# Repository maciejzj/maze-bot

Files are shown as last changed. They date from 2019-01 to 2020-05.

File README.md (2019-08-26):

# MazeBot
Arduino/ATMega based mobile wheeled robot with DC motors controllers, created for a project at Silesian University of Technology.

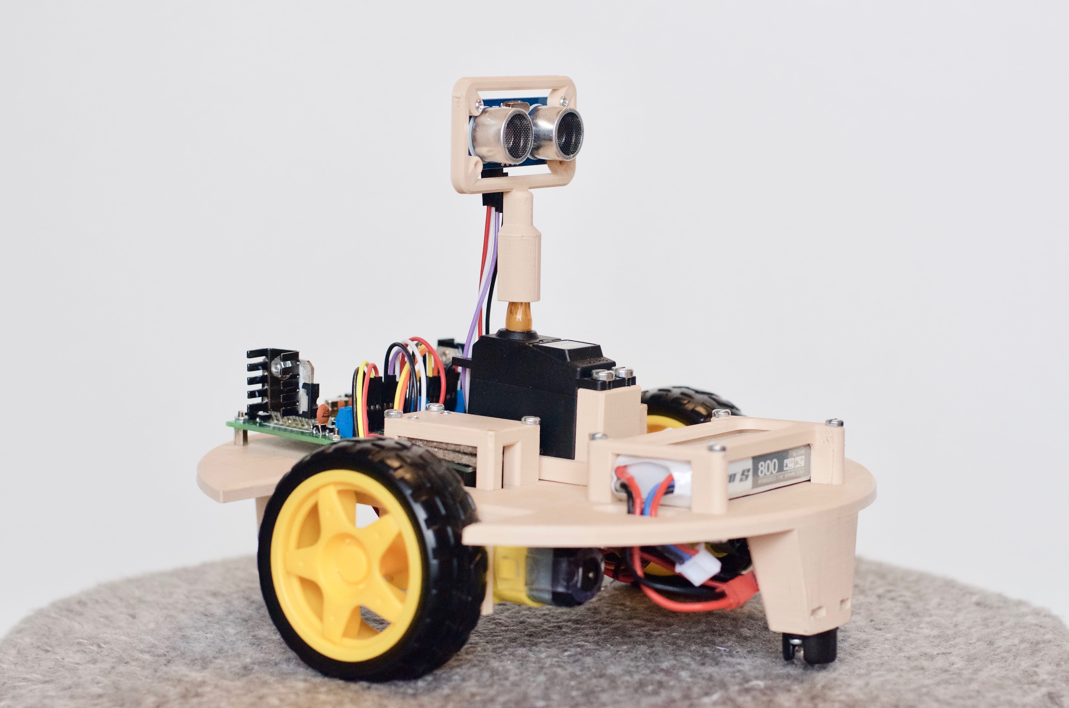
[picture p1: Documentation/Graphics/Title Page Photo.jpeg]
mazebot_demo_photo


The construction is actuated by DC motors. The robot avoids obstacles using an ultrasonic sensor mounted on top of a servo. The robot features a PI controller for synchronisation of the velocity of wheels and a cascade controller for precise turning. These control systems provide greater accuracy of movement, even with the most basic DC motors available.

The project consists of making a custom Arduino Leonardo clone PCB and designing a 3D printable chassis for the construction. Code is implemented using Arduino libraries and the bootloader.

The code and Autodesk Eagle files are stored in the GitHub repository, Autodesk Fusion 360 project files can be accessed using [Autodesk cloud mechanisms](https://a360.co/2U4947x).

Feel free to check out the documentation and [project report](https://raw.githubusercontent.com/MaciejZj/MazeBot/16cebf032a5ea0aaa41a32081933f3ef379c02ca/Documentation/POLSL_Project_Report_PL.pdf) in Polish.

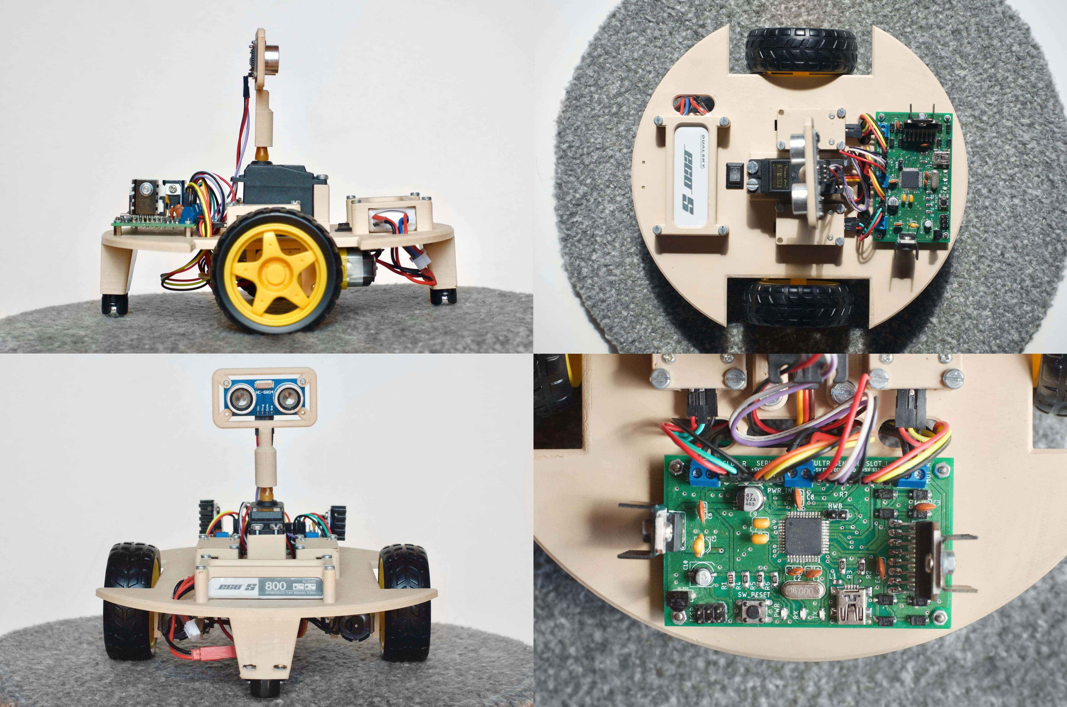
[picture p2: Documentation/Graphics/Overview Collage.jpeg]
mazebot_photo_collage


The project uses modified [nonblocking ultrasonic Arduino library](https://github.com/jazzycamel/arduino).

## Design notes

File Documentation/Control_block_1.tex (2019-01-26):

\documentclass{standalone}

\usepackage{tikz}
\usetikzlibrary{shapes, arrows}
\usetikzlibrary{arrows.meta, positioning}
\begin{document}

% Define styles
\tikzstyle{block} = [draw, rectangle, 
    minimum height=3em, minimum width=3em]
\tikzstyle{sum} = [draw, circle, inner sep=5pt, node distance=2cm]
\tikzstyle{point} = [coordinate]
\tikzstyle{pinstyle} = [pin edge={to-,thin,black}]

\begin{tikzpicture}[auto, node distance=2cm, >=latex']
	\node [point, name=input] {};
	\node [block, below of=input, label={\small Zadajnik}] (master_encoder) {Master encoder};
	\node [block, below of=master_encoder] (differ_master) {
		\begin{tabular}{c}
			Zamiana \\ $ \alpha \rightarrow \omega $
		\end{tabular}};
	\node [sum, right of=differ_master] (sum) {};
	\node [block, right of=sum, xshift=-0.5cm] (kp) {$ k_p $};
	\node [block, right of=kp, yshift=+1.25cm, xshift=0.25cm, label={\small Człon P regulatora}] (one) {$ 1 $};
	\draw [->] (kp) |- node[name=con_one] {} (one);
	\node [block, right of=kp, yshift=-1.25cm, xshift=0.25cm, label={\small Człon I regulatora}] (int) {$ \frac{1}{sT_I} $};
	\draw [->] (kp) |- node[name=con_int] {} (int);
	\node [sum, right of=sum, xshift=4cm] (sum_con) {};
	\node [block, right of=sum_con, xshift=0.25cm] (system) {Obiekt SWPS};
	\draw [->] (sum_con) -- node[name=u] {$u$} (system);
	\node [point, right of=system] (point) {};
	\node [block, below of=u, yshift=-1cm] (slave_encoder) {Slave encoder};
	\node [block, left of=slave_encoder, xshift=-1.75cm] (differ_slave) {
		\begin{tabular}{c}
			Zamiana \\ $ \alpha \rightarrow \omega $
		\end{tabular}};
		
	\draw [->] (master_encoder) -- node {$\alpha_a$} (differ_master);
	\draw [->] (differ_master) -- node {$\omega_a$} (sum);
	\draw [->] (sum) -- node {$e$} (kp);
	\draw [->] (system) -- node [name=y] {$\alpha_s$}(point);	
	\draw [->] (y) |- (slave_encoder);
	\draw [->] (one.east) -| (sum_con);
	\draw [->] (int) -| (sum_con);
	\draw [->] (slave_encoder) -- (differ_slave);
	\draw [->] (differ_slave) -| node[pos=0.99] {$-$} 
		node [near end] {$\omega_s$} (sum);
	
\end{tikzpicture}

\end{document}

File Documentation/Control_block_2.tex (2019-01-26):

\documentclass{standalone}

\usepackage{tikz}
\usetikzlibrary{shapes, arrows}
\usetikzlibrary{arrows.meta, positioning}
\begin{document}

% Define styles
\tikzstyle{block} = [draw, rectangle, 
    minimum height=3em, minimum width=3em]
\tikzstyle{sum} = [draw, circle, inner sep=5pt, node distance=2cm]
\tikzstyle{point} = [coordinate]
\tikzstyle{pinstyle} = [pin edge={to-,thin,black}]

\begin{tikzpicture}[auto, node distance=2cm, >=latex']
	\node [point, name=input] {};
	\node [block, below of=input, label={\small Zadajnik}] (master_encoder) {Master encoder};
	\node [block, below of=master_encoder] (differ_master) {
		\begin{tabular}{c}
			Zamiana \\ $ \alpha \rightarrow \omega $
		\end{tabular}};
	\node [block, right of=differ_master, xshift=2cm, yshift=-2cm] (sa) {$ s^{-1} $};
	\node [block, below of=sa] (ss) {$ s^{-1} $};
	\node [sum, above of=sa, xshift=-1.5cm] (sum_kp) {};
	\node [block, right of=sum_kp, xshift=1.5cm, label={\small Człon P regulatora}] (kp) {$ k_p $};
	\node [sum, above of=sa, xshift=-1.5cm] (sum_kp) {};
	\node [sum, right of=ss] (sum_I) {};
	\node [block, right of=sum_I, label={\small Człon I regulatora}] (kI) {$\frac{k_p}{T_I}$};
	\node [sum, right of=kI, yshift=2cm] (sum_con) {};
	\node [block, right of=sum_con, xshift=0.25cm] (system) {Obiekt SWPS};
	\draw [->] (sum_con) -- node[name=u] {$u$} (system);
	\node [block, below of=u, yshift=-2.2cm] (slave_encoder) {Slave encoder};
	\node [point, right of=system] (point) {};
	\draw [->] (system) -- node [name=y] {$\alpha_s$}(point);	
	\draw [->] (y) |- (slave_encoder);
	\node [block, below of=ss] (differ_slave) {
		\begin{tabular}{c}
			Zamiana \\ $ \alpha \rightarrow \omega $
		\end{tabular}};

	\draw [->] (master_encoder) -- node {$\alpha_a$} (differ_master);
	\draw [->] (differ_master) -- node {$\omega_a$} (sum_kp);
	\draw [->] (sa.east) -| node {$\alpha_a$} (sum_I);
	\draw [->] (differ_master.south) |- node[near end] {$\omega_a$} (sa);
	\draw [->] (sum_kp) -- node {$e_\omega$} (kp);
	\draw [->] (ss) -- node[xshift=0.5cm, yshift=-0.5cm] {$-$} 
		node {$\alpha_s$} (sum_I);
	\draw [->] (kI) -| node {} (sum_con);
	\draw [->] (kp) -| node {} (sum_con);
	\draw [->] (sum_I) -- node {$e_\alpha$} (kI);
	\draw [->] (slave_encoder) -- node {$\alpha_s$} (differ_slave);
	\draw [->] (differ_slave) -- node {$\omega_s$} (ss);
	\draw [->] (differ_slave) -| node[pos=0.99] {$-$} 
		node [near end] {$\omega_s$} (sum_kp);
	
\end{tikzpicture}

\end{document}

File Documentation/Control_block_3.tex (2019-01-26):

\documentclass{standalone}

\usepackage{tikz}
\usetikzlibrary{shapes, arrows}
\usetikzlibrary{arrows.meta, positioning}
\begin{document}

% Define styles
\tikzstyle{block} = [draw, rectangle, 
    minimum height=3em, minimum width=3em]
\tikzstyle{sum} = [draw, circle, inner sep=5pt, node distance=2cm]
\tikzstyle{point} = [coordinate]

\begin{tikzpicture}[auto, node distance=2cm, >=latex']
	\node [point, name=input] {};
	\node [block, below of=input, label={\small Zadajnik}] (master_encoder) {Master encoder};
	\node [block, right of=master_encoder, xshift=1cm] (sm) {$s$};
	\node [sum, right of=sm, xshift=-0.25cm] (sum_kp) {};
	\node [block, below of=sm, yshift=0.25cm] (ss) {$s$};
	\node [sum, below of=sum_kp, yshift=-1.5cm] (sum_I) {};
	\node [block, right of=sum_kp, xshift=-0.25cm, label={\small Człon P regulatora}] (kp) {$k_p$};
	\node [block, right of=sum_I, xshift=-0.25cm,  label={\small Człon I regulatora}] (kI) {$\frac{k_p}{T_I}$};
	\node [sum, right of=kp] (sum_con) {};
	\node [block, right of=sum_con, xshift=0.25cm] (system) {Obiekt SWPS};
	\draw [->] (sum_con) -- node[name=u] {$u$} (system);
	\node [point, right of=system] (point) {};
	\node [block, below of=sum_I] (slave_encoder) {Slave encoder};
	\node [point, above of=sum_con] (open_u) {};
	
	\draw [->] (master_encoder) -- node {$\alpha_a$} (sm);
	\draw [->] (sm) -- node {$\omega_a$} (sum_kp);
	\draw [->] (master_encoder) |- node[xshift=1cm] {$\alpha_a$} (sum_I);
	\draw [->] (sum_kp) -- node {$ e_\omega $} (kp);
	\draw [->] (sum_I) -- node {$ e_\alpha $} (kI);
	\draw [->] (ss) -| node[pos=0.99] {$-$} 
		node [near end] {$\omega_s$} (sum_kp);
	\draw [->] (kp) |- node {} (sum_con);
	\draw [->] (kI) -| node {} (sum_con);
	\draw [->] (open_u) -- node {$ u_o $} (sum_con);
	\draw [->] (system) -- node [name=y] {$\alpha_s$}(point);
	\draw [->] (y) |- (slave_encoder);
	\draw [->] (slave_encoder) -- node[pos=0.99] {$-$} 
		node [near end] {$\alpha_s$} (sum_I);
		\draw [->] (slave_encoder) -| node [yshift=0.89cm] {$\alpha_s$} (ss);
		
\end{tikzpicture}

\end{document}

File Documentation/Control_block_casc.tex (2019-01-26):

\documentclass{standalone}

\usepackage{tikz}
\usetikzlibrary{shapes, arrows}
\usetikzlibrary{arrows.meta, positioning}
\begin{document}

% Define styles
\tikzstyle{block} = [draw, rectangle, 
    minimum height=3em, minimum width=6em]
\tikzstyle{sum} = [draw, circle, inner sep=5pt, node distance=2.5cm]
\tikzstyle{point} = [coordinate]

\begin{tikzpicture}[auto, node distance=2.5cm, >=latex']
	\node [point, name=input] {};
	\node [block, left of=input, label=\small{\begin{tabular}{c}
		Zadajnik \\
		Zamiana kąta skrętu \\
		na liczbę slotów
	\end{tabular}}] (func) {$ f \left( x \right) $};
	\node [sum, left of=func] (sum_ext) {};
	\node [block, left of=sum_ext, label=\small{Regulator położenia}] (con_ext) {$ P \left( s \right) $};
	\node [sum, left of=con_ext] (sum_int) {};
	\node [block, left of=sum_int, label=\small{Regulator prędkości}] (con_int) {$ PI \left( s \right) $};
	\node [block, below of=con_int] (system) {Obiekt SWPS};
	\node [block, below of=con_ext] (int) {$ s^{-1} $};
	
	\draw [->] (input) -- node {$ \beta $} (func);
	\draw [->] (func) -- node {$ \alpha_w $} (sum_ext);
	\draw [->] (sum_ext) -- node {$ e_{\alpha} $} (con_ext);
	\draw [->] (con_ext) -- node {$ \omega_w $} (sum_int);
	\draw [->] (sum_int) -- node {$ e_\omega $} (con_int);
	\draw [->] (con_int) -- node {$ u $} (system);
	\draw [->] (system) -- node {} (int);
	\draw [->] (system) -| node[pos=0.99] {$-$} 
		node [near end] {$\omega$} (sum_int);	
	\draw [->] (int) -| node[pos=0.99] {$-$} 
		node [near end] {$\alpha$} (sum_ext);

\end{tikzpicture}

\end{document}

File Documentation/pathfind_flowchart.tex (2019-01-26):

\documentclass{standalone}

\usepackage{tikz}
\usetikzlibrary{shapes, arrows}
\usetikzlibrary{arrows.meta, positioning}
\begin{document}

% Define styles
\tikzstyle{startstop} = [rectangle, rounded corners, minimum width=3cm, minimum height=1cm,text centered, draw=black]
\tikzstyle{process} = [rectangle, minimum width=3cm, minimum height=1.25cm, text centered, draw=black]
\tikzstyle{decision} = [diamond, aspect=3, minimum width=3cm, minimum height=1cm, text centered, draw=black]

\begin{tikzpicture}[auto, node distance=2cm, >=latex']
	\node (start) [startstop] {Start};
	\node (rand) [process, below of=start] {
	\small{\texttt{int direction = random(RIGHT, LEFT + 1);}}
	};
	\node (turn) [process, below of=rand] {
	\small{\texttt{turnServoSensor(direction);}}
	};
	\node (pathfind) [decision, below of=turn, yshift=-1cm] {
	\small{\texttt{sensor.probeRange()<SAFE\_DIST;}}
	};
	\node (return) [process, right of=pathfind, yshift=-2.5cm, xshift=2.5cm] {
	\begin{tabular}{c}
		\small{\texttt{direction = !direction;}} \\ 
		\small{\texttt{turnServoSensor(direction);}}
	\end{tabular}
	};
	\node (repathfind) [decision, below of=return, yshift=-1cm] {
	\small{\texttt{sensor.probeRange()<SAFE\_DIST;}}
	};
	\node (back) [process, right of=repathfind, yshift=-2.5cm, xshift=2.5cm] {
	\small{\texttt{direction = BACK;}}
	};
	\node (finish) [process, left of=back, xshift=-11.5cm] {
	\begin{tabular}{c}
		\small{\texttt{turnServoSensor(FRONT);}} \\ 
		\small{\texttt{return direction;}}
	\end{tabular}
	};
	\node (stop) [startstop, below of=finish] {Stop};
	
	\draw [->] (start) -- node {} (rand);
	\draw [->] (rand) -- node {} (turn);
	\draw [->] (turn) -- node {} (pathfind);
	\draw [->] (pathfind.west) -| node[yshift=0.25cm, xshift=0.25cm] {No} (finish);
	\draw [->] (pathfind) -| node[yshift=0.25cm, xshift=-1cm] {Yes} (return);
	\draw [->] (return) -- node {} (repathfind);
	\draw [->] (repathfind) -| node[yshift=0.25cm, xshift=-1cm] {Yes} (back);
	\draw [->] (repathfind) -| node[yshift=0.25cm, xshift=4cm] {No} (finish);
	\draw [->] (back) -- node {} (finish);
	\draw [->] (finish) -- node {} (stop);
	
\end{tikzpicture}

\end{document}

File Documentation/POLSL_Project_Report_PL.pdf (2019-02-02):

## Projekt Systemy Mikroprocesorowe

MazeBot
Robot unikający przeszkód z regulacją napędu silników prądu stałego
Maciej Ziaja | Bartosz Staszulonek
| 2 lutego 2019

### Spis treści

1 Wstęp | 2
2 Organizacja projektu | 2
3 Budowa prototypu, analiza problemów | 3
4 Projekt układu elektronicznego | 4
5 Projekt podwozia robota | 10
6 Synteza układów regulacji | 11
7 Implementacja programistyczna | 22
8 Wykorzystane technologie | 25
9 Perspektywy rozwoju, podsumowanie | 26

### 1 Wstęp

### 1.1 Abstrakt

Projekt polega na konstrukcji mobilnego robota, który unika przeszkód. Układ porusza się na dwóch kołach oraz wykrywa elementy otoczenia używając czujnika ultradźwiękowego zamocowanego na wieży serwomechanizmu. Platforma robota napędzana jest za pomocą pary silników prądu stałego, których kąt obrotu jest odczytywany przez czujniki szczelinowe. W celu zwiększenia precyzji działania konstrukcji zbudowano układy regulacji prędkości silników. Wykonano dwa typy układów regulacji: synchronizujący prędkość obrotu obu silników, w celu zachowania kierunku jazdy na wprost, oraz kaskadowy układ regulacji skrętu platformy robota. Układ regulacji skrętu robota przypomina zasadą działania prosty serwomechanizm. Przedstawiono metodę identyfikacji obiektu regulacji i strojenia regulatorów z użyciem linii pierwiastkowych. Na potrzeby projektu wykonano także schemat układu elektronicznego i zrealizowano go w postaci obwodu drukowanego pcb. Zaprojektowano także podwozie robota i wydrukowano je w technologii 3D.

### 1.2 Cel i zakres projektu

Projekt obejmował budowę platformy bazującej na mikroprocesorze z serii ATmega32, obsługującym peryferia:

- czujnika ultradźwiękowego wykrywającego przeszkody,
- wieży serwomechanizmu, na której zamontowany jest czujnik i która kieruje go w różne strony,
- silników prądu stałego stanowiących napęd platformy,
- czujników szczelinowych odczytujących kąt obrotu kół platformy,
- odbiornika podczerwieni pozwalającego na zdalne wyłączenie robota, jeśli ten się oddali.

Współpraca wymienionych komponentów pozwala robotowi na unikanie przeszkód. Działanie robota powinno polegać na jeździe przed siebie, do czasu napotkania przeszkody. W momencie wykrycia przeszkody robot powinien się zatrzymać, a następnie zbadać czy w jego otoczeniu znajduje się niezagrodzona droga i skierować się w jej stronę. Prototyp układu wykonano z użyciem układu Arduino Leonardo. Na wykonanym prototypie wykonano testy współpracy komponentów i wyciągnięto wnioski dotyczące budowy finalnej konstrukcji oraz wymaganych parametrów komponentów. Działanie prototypu prowadziło do następujących decyzji projektowych, które podyktowały dalszy tok projektu i jego zakres:

- w celu wydajnego wykorzystania przestrzeni na platformie zdecydowano się na wykonanie własnego układu elektronicznego i obwodu drukowanego,
- zaprojektowano własne podwozie dopasowane do używanych peryferiów,
- wykonano układy regulacji jazdy na wprost oraz skręcania platformy.

### 2 Organizacja projektu

### 2.1 Harmonogram

Projekt należało zrealizować w przeciągu 4 miesięcy. Proces jego wykonania składał się z dwóch części: testów komponentów wraz z budową prototypu oraz konstrukcji finalnego układu, na podstawie wniosków wyciągniętych z testów konstrukcji prototypowej. Tabela 1 przedstawia ramowy rozkład pracy w czasie.

Termin | Zakres pracy
01.10.2018 - 20.10.2018 | Zebranie komponentów układu, ustalenie zakresu prac
20.10.2018 - 01.11.2018 | Test komponentów i peryferiów z użyciem Arduino Leonardo
01.11.2018 - 14.11.2018 | Budowa prototypu, programowanie głównej logiki programu
14.11.2018 - 01.12.2018 | Projekty obwodu drukowanego PCB i podwozia
01.12.2018 - 20.12.2018 | Synteza i oprogramowanie układów regulacji
20.12.2018 - 01.01.2019 | Złożenie finalnego układu
01.01.2019 - 20.01.2019 | Strojenie układów regulacji, budowa dokumentacji

Tabela 1: Harmonogram pracy

### 2.2 Budżet

Budżet projektu wynosił 150 złotych, najbardziej znaczącym wydatkiem w projekcie było wydrukowanie obwodu elektronicznego. Zaletą projektu jest modułowość konstrukcji podwozia, przez co elementy można łatwo wymieniać w przypadku chęci zastosowania droższych lub tańszych komponentów. Finalny kosztorys projektu przedstawia tabela 2, dokładny spis elementów elektronicznych na obwodzie drukowanym przedstawiono w dokumencie csv załączonym do plików projektu. Całkowity koszt komponentów projektu wyniósł 149,86 złotych.

Komponent | Koszt | Producent | Dostawca
Obwód drukowany PCB | 53,00 PLN | Elpin PCB | Elpin PCB
ATmega32u4 | 15,91 PLN | Microchip Atmel | TME Electronic Components
Elementy pasywne | v7,50 PLN | Panasonic, ST Electronics | TME Electronic Components
Elementy aktywne | v4,00 PLN | ST Electronics | TME Electronic Components
Silniki prądu stałego z kołami i dyskami enkoderów | 19,90 PLN | Dagu | Botland
Serwomechanizm | 6,90 PLN | Tower Pro | Botland
Ultradźwiękowy czujnik odległości HC-SR04 | 7,90 PLN | Elec | Botland
Czujniki szczelinowe | 9,90 PLN | Vishay | Botland
Odbiornik podczerwieni TSOP4836 - 36khz | 2,95 PLN | Vishay | Botland
Bateria Li-Pol | 21,90 PLN | Dualsky | Botland

Tabela 2: Kosztorys, rozdysponowanie budżetu

### 3 Budowa prototypu, analiza problemów

Realizację projektu zaczęto od zgromadzenia peryferiów koniecznych do realizacji konstrukcji robota. W pierwszej fazie prototypowania komponenty testowano osobno używając Arduino Leonardo. Zapoznano się z ich praktycznymi możliwościami i działaniem dostępnych bibliotek.
Następnie połączono wszystkie komponenty i przeprowadzono ich jednoczesne testy oraz zmierzono zasilanie używając multimetru wraz z zasilaczem regulowanym. Elementy prototypowe umieszczono na platformie testowej i oceniono działanie konstrukcji. Okazało się, że działanie robota jest możliwe, ale sterowanie silnikami w torze otwartym nie było wystarczająco precyzyjne aby unikać przeszkód. Przy symetrycznym wysterowaniu silników robot nie poruszał się w kierunku prostym, różnice w działaniu poszczególnych silników są zbyt duże by pracowały one symetrycznie co jest wymagane by platforma jechała na wprost. Skręcanie platformy o zadany kąt również okazało się nieprecyzyjne, obroty o na przykład 90 stopni w prawo były mało powtarzalne i obarczone dużym błędem. Zdecydowano się na syntezę układów regulacji, aby wyeliminować te problemy.
Testy platformy prototypowej pokazały także, że złożoność układu jest zbyt duża aby budować go na płytce stykowej/prototypowej. Dodatkowo serwomechanizm, który jest bardzo wrażliwy na zakłócenia zasilania, działał źle gdy był połączony przez wiele kabli, które razem tworzyły dużą rezystancję. Obserwacje te skłoniły nas do zaprojektowania własnego obwodu drukowanego, który mieściłby wszystkie potrzebne komponenty elektroniczne na małej przestrzeni. Konstrukcja mechaniczna platformy prototypowej okazała się mało solidna i nie była dostosowana do używanych przez nas modułów elektronicznych. W celu zwiększenia wytrzymałości i schludności wykonania układu zdecydowano się na projekt własnego podwozia robota.

### 4 Projekt układu elektronicznego

### 4.1 Działanie i uzasadnienie doboru elementów elektronicznych

### 4.1.1 Mikroprocesor ATmega32u4

Centralnym elementem robota jest mikroprocesor avr o architekturze risc. Ośmiobitowe mikroprocesory ATmega są popularnym wyborem przy konstrukcji układów wbudowanych w przemyśle i urządzeniach elektronicznych o niedużym stopniu wymaganej wydajności. Ich zaletą jest powszechność oraz fakt, że na procesorach z tej rodziny bazuje popularna platforma Arduino, w ramach której dostępny jest szeroki zakres bibliotek programistycznych do obsługi peryferiów.
Przy wyborze konkretnego modelu mikroprocesora kierowaliśmy się następującymi wymaganiami:
- obsługa czterech przerwań zewnętrznych:
1. pochodzących z enkodera lewego koła,
2. pochodzących z enkodera prawego koła,
3. pochodzących z czujnika ultradźwiękowego,
4. pochodzących z odbiornika podczerwieni,
- obsługa trzech wyjść PWM, za pomocą liczników w celu:
1. sterowania prędkością lewego silnika prądu stałego,
2. sterowania prędkością prawego silnika prądu stałego,
3. sterowania położeniem serwomechanizmu, na którym zamontowany jest czujnik ultradźwiękowy,
- możliwość użycia sumarycznie dwunastu wejść wyjść cyfrowych do komunikacji z peryferiami,
- pożądana jest wbudowana obsługa komunikacji szeregowej za pomocą interfejsu USB w celu łatwego debugowania układu i zdjęcia pomiarów dynamiki układu przy identyfikacji obiektu regulacji i strojeniu regulatorów,
- powyższe wymagania powinny być spełnione przy użyciu bootloadera i bibliotek Arduino.

Powyższe wymagania spełnia mikroprocesor ATmega32u4 firmy Atmel, co można wywnioskować z jego dokumentacji [6]. Na tym procesorze bazuje układ Arduino Leonardo, który wykorzystano przy konstrukcji prototypu. Mikroprocesor ATmega32u4 z użyciem bibliotek Arduino pozwala na używanie do pięciu przerwań zewnętrznych oraz siedmiu kanałów generujących sygnały pwm.
Istotne jest, że kanały pwm są obsługiwane przez cztery oddzielne liczniki. Biblioteki Arduino (szczególnie obsługi serwomechanizmu) wchodzą łatwo w konflikty i korzystają z liczników w sposób uniemożliwiający ich współdzielenie przy generowaniu sygnałów pwm. Dlatego przy doborze mikroprocesora i rozdysponowaniu jego zasobów starano się, aby serwomechanizm był obsługiwany przez oddzielny licznik, który nie jest dzielony z innymi funkcjami układu. Oznacza to, że pin sterujący serwem nie powinien generować sygnałów z użyciem tego samego licznika, co inne kanały PWM, aby uniknąć konfliktów bibliotek Arduino.
Wybrany model mikroprocesora jest dostępny tylko w obudowach powierzchniowych qfp (Quad

Flat Package), przy wyborze tej jednostki należy pamiętać, że wymaga ona umiejętności precyzyjnego lutowania. Procesor może pracować przy zasilaniu 5 V, jest to dogodna wartość ponieważ reszta peryferiów w układzie ma takie same napięcie zasilania.

### 4.1.2 Silniki prądu stałego

Ze względu na ograniczenia budżetowe zdecydowano się na jedne z najtańszych dostępnych silników, wyprodukowane przez firmę Dagu. Silniki prądu stałego oferują największe momenty siły przy małych obrotach, nadają się dobrze do napędzania i przyspieszania platform robotów, oferują możliwość płynnego sterowania. Ich wadą jest fakt, że bez dodatkowego układu czujników nie można określić ich kąta obrotu. Należy mieć na uwadze, że ze względu na obecność komutatora i szczotek silniki prądu stałego zużywają się w czasie pracy. Parametry wybranych przez nas silników są następujące:

- maksymalne napięcie zasilania: 6 V,
- moment obrotowy: 0.8 kg · cm, 0.78 N · m,
- obroty silnika bez obciążenia: (90 ± 10) obr
min,
- pobór prądu silnika bez obciążenia: 190 mA (max. 250 mA),
- pobór prądu silnika przy zatrzymanym wale: 1 A.

Do silników przymocowano koła o parametrach:

- średnicy: 65 mm,
- szerokości: 30 mm.

### 4.1.3 Sterownik silników prądu stałego - mostek h

Najbardziej popularnym sposobem sterowania silnikami prądu stałego jest użycie mostka h. Jest to układ składający się z czterech tranzystorów polowych, których dreny i źrodła są odpowiednio połączone ze sterowanym silnikiem. Para tranzystorów połączona z tą samą szczotką silnika ma złączone bramki, ale przeciwny stan otwarcia. Złączone bramki są wyprowadzone z układu i stanowią wejścia sterowania. W zależności od tego na które z wejść podamy stan wysoki przez jeden z tranzystorów z każdej pary będzie płynął prąd, powodując obroty silnika w odpowiednim kierunku. Układem elektronicznym, który zawiera w sobie dwa mostki h, co pozwala na sterowanie parą silników, jest L298N. Dodatkowo układ posiada dodatkowe tranzystory do sterowania prędkością silników za pomocą sygnału pwm, który stopniowo otwiera i domyka tranzystor polowy przepuszczający sygnały wejściowe. Parametry sterownika są następujące:

- maksymalne napięcie zasilania silników: 45 V,
- napięcie części logicznej: od 4,5 V do 7 V,
- maksymalny prąd zasilający silnik: 2 A.

Sterownik dostępny jest w obudowie przewlekanej Multiwatt15, jego producentem jest firma STMicroelectronics. Porównując parametry mostka, zawarte w dokumentacji [7] z parametrami silników możemy stwierdzić, że jest on wystarczający do ich wysterowania.

### 4.1.4 Czujnik ultradźwiękowy

Najbardziej popularnym i łatwo dostępnym miernikiem odległości jest czujnik ultradźwiękowy HC-SR04. Czujniki ultradźwiękowe mierzą odległość na podstawie czasu, który jest potrzebny fali ultradźwiękowej na dotarcie do przeszkody i powrót do czujnika po jej odbiciu. Pomiar czujnikiem rozpoczyna się od podania na wejście trig stanu wysokiego przez 10 µs. Powoduje to wygenerowanie przez czujnik ciągu ośmiu sygnałów ultradźwiękowych o częstotliwości 40 kHz. Po odbiciu sygnału od przeszkody i jego powrocie do czujnika odległość można obliczyć według wzoru 1, gdzie:

- d to odległość mierzona,
- th to czas trwania stanu wysokiego,
- vs to prędkość rozchodzenia się fali dźwiękowej w powietrzu, typowo 340 m s⁻¹ .

d =

th · vs
2

(1)

Model czujnika HC-SR04, zgodnie z dokumentacją [8] charakteryzuje się następującymi parametrami:

- napięcie zasilania: 5 V,
- średni pobór prądu: 15 mA,
- zakres pomiarowy: od 2 cm do 200 cm,
- częstotliwość pracy: 40 kHz,
- wymiary: 45 × 20 × 15 mm.

Zasilanie czujnika i jego zakres pracy są odpowiednie dla projektu. Przeszkody, które chcemy wykrywać będą znajdywały się w odległości parunastu centymetrów od robota, czyli w zakresie pracy czujnika. Należy mieć na uwadze, że czujniki ultradźwiękowe wykrywają najlepiej duże przeszkody. Dodatkowo istotne jest, że pomiar czujnika ultradźwiękowego trwa w czasie, przebycie odpowiedniej drogi przez falę ultradźwiękową nie jest natychmiastowe. Kwestia ta zostanie wzięta pod uwagę w czasie tworzenia oprogramowania.

### 4.1.5 Serwomechanizm

Aby umożliwić robotowi kierowanie czujnika odległości w różnych kierunkach, został on zamieszczono na wieży serwomechanizmu. Ponieważ wymagamy aby czujnik mógł być skierowany w lewo, prawo oraz na wprost wystarczające jest serwo 180 stopni. Waga czujnika ultradźwiękowego jest znikoma, dlatego serwomechanizm można wybrać kierując się jak najniższą ceną.

### 4.1.6 Odbiornik podczerwieni TSOP4836

Robota wyposażono w odbiornik podczerwieni ułatwiający jego zatrzymanie. W celu łatwej współpracy z domowymi pilotami na podczerwień należało wybrać odbiornik wspierający popularne formaty: NEC Code, Toshiba Micom Format, Sharp Code, RC5 Code, RC6 Code, R–2000 Code. . . .
Wybraliśmy odbiornik TSOP4836 pracujący z falami o częstotliwości 36 kHz. Zgodnie z dokumentacją [9] firmy Vishay odbiornika należy go zabezpieczyć kondensatorem filtrującym i rezystorem. Parametry odbiornika są następujące:
- napięcie zasilania: od 4,5 V do 5,5 V,
- średni pobór prądu: 1,5 mA.

Przy projektowaniu obwodu drukowanego i lutowaniu odbiernika należy zwrócić uwagę na jego wyprowadzenia. Wiele czujników podczerwieni o identycznych obudowach i podobnych parametrach ma bardzo różne kolejności wyprowadzeń.

### 4.1.7 Stabilizator napięcia L7805CV

W konstruowanym projekcie wszystkie układy logiczne zasilane są napięciem 5 V, natomiast silniki zasilane są napięciem 7,4 V. Wynika stąd, że najlepiej zastosować baterię siedmiowoltową, a zasilanie części logicznej dostarczać poprzez regulator napięcia. Najbardziej popularnym regulatorem jest układ 7805, produkowany przez firmę STMicroelectronics [10]. W wersji cv jego parametry są następujące:

- maksymalne napięcie wejściowe: 35 V,

- napięcie wyjściowe: 5 V (z dokładnością 2 %),
- maksymalny prąd wyjściowy: 1,5 A.

Stabilizator jest dostępny w różnych obudowach, przewlekanych i powierzchniowych. Ze względu na łatwość montażu, dostępność i możliwość zamontowania radiatora wybraliśmy model w obudowie przewlekanej TO-220. Po porównaniu parametrów stabilizatora z parametrami komponentów, które zasili można stwierdzić, że jest on wystarczający by spełnić zapotrzebowania projektu.

### 4.1.8 Akumulator

Testy pokazały, że przy zasilaniu 7,4 V układ pobiera prąd do 0,3 A, co dostarcza nam informacji potrzebnych do doboru baterii dla robota. Zdecydowano się na zastosowanie akumulatora litowopolimerowego firmy Dualsky. Jego najważniejsze parametry są następujące:

- akumulator składa się z dwóch ogniw Li-pol,
- napięcie nominalne: 7,4 V,
- pojemność: 800 mAh,
- prąd rozładowania ciągły: 20 A,
- wbudowane przewody ze wtykiem jst.

### 4.1.9 Elementy pasywne

Użyte komponenty elektroniczne wymagają użycia kondensatorów filtrujących, zastosowano kondensatory o pojemnościach podanych w dokumentacjach filtrowanych elementów. Kondensatory ceramiczne są umieszczone w obudowach przewlekanych, starano się dobrać kondensatory elektrolityczne w obudowach powierzchniowych, aby zredukować miejsce, którą zajmują. Spis wszystkich elementów układu, w tym elementów pasywnych znajduje się w osobnym pliku csv dostępnym na stronie projektu.

### 4.2 Schemat układu elektronicznego

Na rysunku 1 przedstawiono utworzony schemat układu elektronicznego. Projekt układu wykonano w programie Autodesk Eagle1
, korzystając z bibliotek komponentów. Centralnym elementem układu jest mikroprocesor ATmega32u4 oznaczony symbolem U3, znajduje się on w polu C3 schematu. Źródłem taktowania mikroprocesora jest zewnętrzny rezonator kwarcowy 16 MHz. Do jego poprawnego działania konieczne są odpowiednie kondensatory. Aby osiągnąć zamierzone taktowanie użyto kondensatorów o pojemności 22 pF. Mikroprocesor zasilono napięciem 5 V, które jest filtrowane kondensatorami 0,1 µF, zasilanie portu USB jest filtrowane kondensatorami 1 µF. Aby ułatwić restartowanie układu, na schemacie umieszczono przycisk, który umożliwia zwieranie pinu reset z ziemią. Jeżeli przycisk jest przytrzymany dostatecznie długo układ mikroprocesorowy zostanie zresetowany. Aby podczas resetu nie doszło do zwarcia obwodu zasilania, dodano rezystor R1. Układ resetu znajduje się w polu B2 schematu.
W polu A2 schematu umieszczono diody sygnalizacyjne. Dioda PWR_LED sygnalizuje obecność napięcia na wyjściu stabilizatora. Diody TX_LED oraz RX_LED są związane z transmisją szeregową, podłączono je tak że są aktywne kiedy wyjścia procesora są w stanie niskim. Dzięki temu diody świecą kiedy transmisja szeregowa nie ma miejsca i sygnalizują tym samym poprawne działanie procesora. Jest to wygodne ponieważ dioda PWR_LED sygnalizuje jedynie obecność zasilania układu, ale nie informuje użytkownika o właściwym uruchomieniu mikroprocesora. Każda z diod podłączona jest przez odpowiedni rezystor ograniczający płynący prąd. W polu C1 znajduje się port USB w wersji micro. Linie portu szeregowego zabezpieczono dławikiem ferrytowym, oraz rezystorami. Do programowania mikroprocesora zastosowano złącze ICSP sześciopinowe, znajdujące się w polu D1 schematu.

1Autodesk Eagle: https://www.autodesk.com/products/fusion-360/overview

POWER SUPPLY ECU - H Bridge ICSP USB STATUS LED ATMEGA32 IR RCV I/O PORTS Mobile robot avoiding obstacles with additional DC motors controllers. Check out more at: https://github.com/MaciejZj/MazeBot 7805TV 0.33uF 0.1uFV5++V GND GND GND L298 +V V5+ GND GND 1F G 1F G 1F G 1F G 1F G 1F G 1F G 1F G GND +V z HM61 ATMEGA32U4-AU Fp22 Fp22 GND V5+ GND GND ICSP k01 GND V5+ 1uF GND 0.1uF GND 1uF GND GND 2222 MACIEJ ZIAJA V5+ k1 GND V5+ k1 V5+ k1 4.7uF V5+ GND V5+ GND V5+ GND V5+ GND 47uV5+ FGND +V GND k01 GND 600Ω/500mA 0.1uF 0.1uF GND V5+ GND VI 1 2 VO 3 U1 C5 C6 SEN_B 15 OUT4 14 OUT3 13 INPUT4 12 ENABLE_B 11 INPUT3 10 VCC 9 GND 8 INPUT2 7 ENABLE_A 6 INPUT1 5 VS 4 OUT2 3 OUT1 2 SEN_A 1 U2 1 D2 D3 D4 D 5 D6 D7 D8 D 1 2 1 Q XTAL2 16 XTAL1 17 GND 15 VCC 14 UVCC 2 UGND 5 D- 3 AVCC 24 PB3(PDO/MISO) 11 PB2(PDI/MOSI) 10 PB1(SCK) 9 PB0(SS) 8 PD7(OC4D/ADC10/T0) 27 PD6(T1/ADC9/OC4D) 26 PD5(XCK/CTS) 22 PD4(ICP1/ADC8) 25 PD3(INT3/TXD1) 21 PD2(INT2/RXD1) 20 PD1(INT1/SDA) 19 PD0(INT0/OC0B/SCL) 18 PC7(ICP3/CLK0/OC4A) 32 PC6(OC3A/OC4A) 31 PB4(ADC11) 28 PB6(OC1B/OC4B/ADC13) 30 PB5(OC1A/ADC12/OC4B) 29 PB7(OC0A/OC1C/RTS) 12 /RESET 13 D+ 4 UCAP 6 PE2(HWB) 33 PF0(ADC0) 41 PF1(ADC1) 40 PF4(ADC4/TCK) 39 PF5(ADC5/TMS) 38 PF6(ADC6/TDO) 37 PF7(ADC7(TDI) 36 PE6(INT.6/AIN0) 1 VBUS 7 GND1 23 AVCC1 44 VCC1 34 AREF 42 GND2 35 GND3 43 U3 1 C 2 C 3 12 4SW_RESET 123456 ICSP1 1 R C7 C8 C9 D+D- VBUS GNIDD USB R2 R3 4 R DEL_ R WP 5 R DEL_XT 6 R DEL_XR VS 3 OUT 1 GND 2 C10 1234 ULTR_SENSOR S123 LOT_R S123 LOT_L 123 SERVO C11 21 PWR_IN 12 MOT_L 12 MOT_R 7 R 12 B WH L1 C3 C4EN_L EN_L EN_R EN_R IN1_L IN1_L IN2_L IN2_L IN1_R IN1_R IN2_R IN2_R SCK SCK SS SS MOSI MOSI MISO MISO RESET RESET AREF UCAP UVCC D- D- D+ D+ SLOT_SENS_2 SLOT_SENS_2 SLOT_SENS_1 SLOT_SENS_1 SERVO SERVO ULTR_TRIG ULTR_TRIG ULTR_ECHO ULTR_ECHO IR_RCV IR_RCV TX XT MOT1_L MOT1_L MOT2_L MOT2_L MOT1_R MOT1_R MOT2_R MOT2_R + MISO +5V SCK MOSI RESET GND Sheet: ABCD 1 2 3 4 5 6 ABCD 1 2 3 4 5 6 MazeBot Main Board 18.01.2019 22:44 1/1 + + Rysunek 1: Schemat układu elektronicznego 8

W polu A5 schematu znajduje się mostek L298. Aby zabezpieczyć układ do jego wyjść silnikowych dodano diody prostownicze skierowane przeciwnie do polaryzacji baterii. W czasie pracy silników na ich uzwojeniu gromadzi się energia w postaci pola magnetycznego. Po zatrzymaniu silników i hamowaniu platformy energia to wróci do układu w postaci płynącego prądu. Dzięki obecności diod układ mostka jest zabezpieczony przez tymi prądami, popłyną one przez diody do baterii. Co więcej, ze względu na polaryzację diod, energia odzyskiwana z silników będzie ładować baterię, tworząc prosty układ aktywnego hamowania. W sekcji io ports znajdują się złącza peryferiów układu.
Komponenty z fabrycznymi wyprowadzeniami przez goldpiny, połączono takimi samymi złączami od strony układu. Silniki i zasilanie są złączone przez konektory arc dokręcane śrubokrętem.

### 4.3 Projekt układu drukowanego

### 4.3.1 Parametry techniczne układu drukowanego

Ze względu na ograniczoną przestrzeń na powierzchni platformy robota zdecydowano się na wykonanie własnego obwodu drukowanego w technologii dwustronnej, z metalizowanymi otworami i soldermaską. W celu zachowania zgodności z procesem technologicznym producenta płytek2 przyjęto następujące

ustawienia drc (Design rules check ):

- grubość laminatu wraz ze ścieżkami: 1,5 mm,
- grubość ścieżek: 0,035 mm,
- odległości między ścieżkami, przelotkami (via) oraz padami: 6 mil,
- odległości ścieżek od krawędzi płytki: 40 mil,
- minimalna odległość otworów: 6 mil,
- minimalna szerokość ścieżki: 6 mil„
- minimalna średnica otworu: 0,35 mm,
- szerokość termoizolacji padów od wylewek (ułatwia lutowanie): 10 mil.

Dwuwymiarowe wizualizacje obwodu drukowanego wykonanego w programie Autodesk Eagle przedstawiają rysunki 2 oraz 3. Przy tworzeniu płytki zastosowano technikę wylewki masy, czyli tworzenia dużych płaszczyzn przewodnika, zamiast prowadzenia poszczególnych ścieżek. Ułatwia to rozmieszczenie połączeń i zmniejsza rezystancję ścieżek masy. Zastosowano materiały zawierające ołów jako bardziej wytrzymałe i łatwiejsze w lutowaniu. W amatorskim lutowaniu nie używa się temperatur przy których wydzielają się trujące opary ołowiu.

### 4.3.2 Rozmieszczenie elementów na powierzchni układu drukowanego

W centralnej części obwodu drukowanego umieszczono mikroprocesor. Rozdysponowanie wyprowadzeń sygnałowych mikroprocesora jest kompromisem między ograniczeniami bibliotek Arduino, możliwościami procesora oraz ilością miejsca dostępnego na płytce. Górną krawędź układu zajmują konektory peryferiów, dolna krawędź została przeznaczona na elementy służące interakcji z użytkownikiem. Płytka została wykonana w technologii mieszanej3
, w celu zaoszczędzenia miejsca starano się używać elementów montowanych powierzchniowo, tam gdzie było to możliwe i wygodne. Podczas prowadzenia ścieżek układu należy mieć na uwadze ich szerokość. Znając parametry techniczne płytki oraz prądy płynące przez poszczególne ścieżki można obliczyć ich minimalną szerokość za pomocą kalkulatorów dostępnych online4
. Obudowę rezonatora kwarcowego oddzielono od powierzchni obwodu wyciętą gumą. Na obudowach elementów aktywnych umieszczono radiatory.

2Elpin: https://www.elpinpcb.com.pl/prototypy/
3To znaczy użyto zarówno elementów przewlekanych jak i montowanych powierzchniowo 4Kalkulator scieżek 4PCB https://www.4pcb.com/trace-width-calculator.html

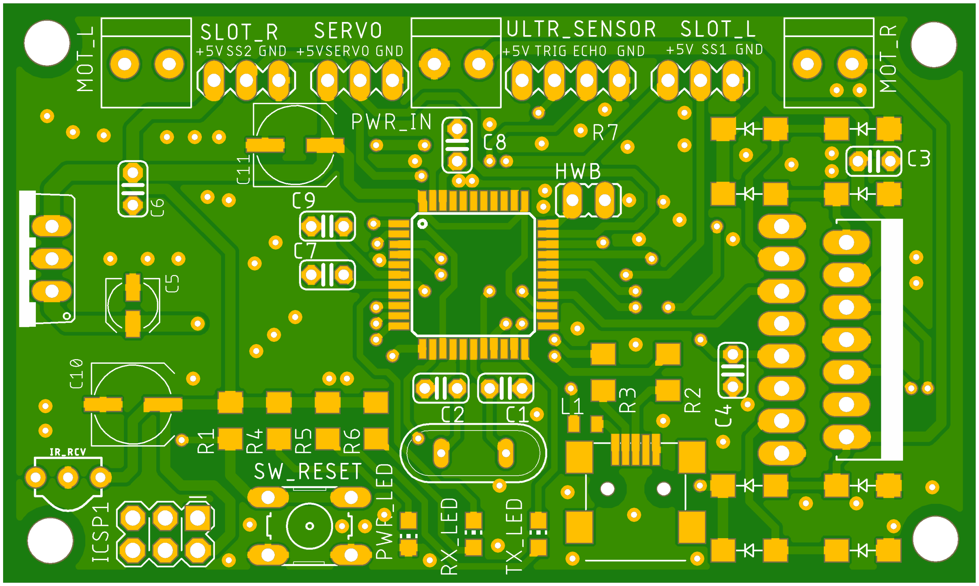
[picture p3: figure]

Rysunek 2: Górna warstwa obwodu drukowanego

### 5 Projekt podwozia robota

W celu zwiększenia trwałości i solidności budowy podwozia zdecydowano się zaprojektować własne oraz wydrukować je w technologii 3D. Do jego modelowania użyto programu Autodesk Fusion 3605 .
Podwozie zaprojektowano tak aby osiągnąć jego modułowość. Platforma robota składa się z osobnych części:
- głównego podwozia z uchwytami na silniki,
- dwóch obudów na czujniki szczelinowe,
- uchwytu na serwomechanizm,
- elementu mocującego czujnik ultradźwiękowy na szczycie serwomechanizmu,
- obudowy baterii.

Obudowy komponentów są łączone z podwoziem za pomocą śrub. Jeżeli zaistniałaby potrzeba wymiany danego komponentu, na przykład serwomechanizmu, wystarczy wydrukować nową obudowę jedynie na wymieniane peryferium. Przy projekcie uwzględniono utworzenie otworów oraz uchwytów na kable. Akumulator litowo-polimerowy jest połączony z obwodem przez przełącznik dwupozycyjny, co pozwala na wyłączenie zasilania. Podwozie wydrukowano w technologii 3D za pomocą posiadanej drukarki, dzięki czemu koszta jego utworzenia są znikome.

5Autodesk Fusion 360: https://www.autodesk.com/products/fusion-360/overview

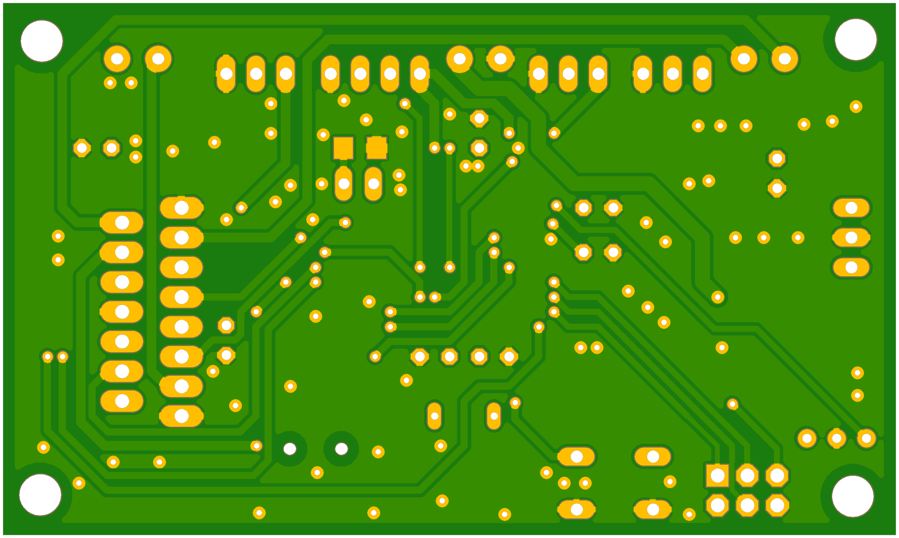
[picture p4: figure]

Rysunek 3: Dolna warstwa obwodu drukowanego

### 6 Synteza układów regulacji

Budowa i testy układu prototypowego wykazały, że bez zastosowania dodatkowych środków układ porusza się w sposób nieprecyzyjny. Zdecydowano się na syntezę układów regulacji w celu poprawienia precyzji działania robota.

### 6.1 Regulator synchronizacji prędkości silników

Bez zastosowania układu regulacji robot nie porusza się prosto przy symetrycznym wysterowaniu lewego i prawego silnika, to znaczy że platforma skręca kiedy nie jest to pożądane. Problem ten jest spowodowany różnicami w wykonaniu poszczególnych silników, niesymetrycznym obciążeniem platformy oraz niedoskonałościami jej konstrukcji. To zagadnienie można próbować rozwiązać następującymi sposobami:

- wyważaniem platformy robota odpowiednimi odważnikami, jest to najgorsze rozwiązanie, nie dające pewnych wyników, jest też zależne od stopnia naładowania baterii, który wpływa na silniki niesymetrycznie,
- sterowaniem pwm w otwartym torze, tak aby uwzględnić niesymetryczność silników, sterowanie należy ustalić drogą eksperymentalną, ta metoda również jest podatna na rozładowanie baterii oraz zmianę obciążenia platformy i inne zakłócenia,
- konstrukcją regulatorów, które na podstawie odczytów z enkoderów szczelinowych synchronizują prędkość silników.

Ze względu na największą pewność efektów, niskie koszty oraz wartość edukacyjną zdecydowano się na rozwiązanie wykorzystujące układy regulacji.

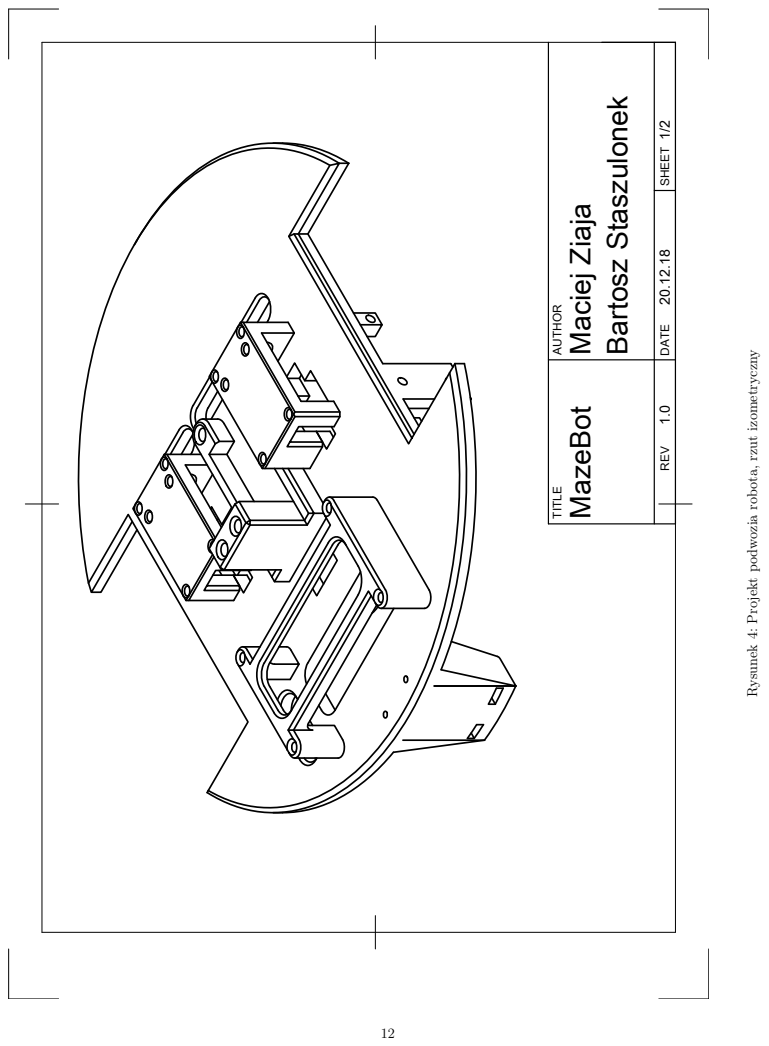
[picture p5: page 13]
TITLE; AUTHOR

Bartosz Staszulonek Rysunek 4: Projekt podwozia robota, rzut izometryczny

REV DATE SHEET

MazeBot Maciej Ziaja

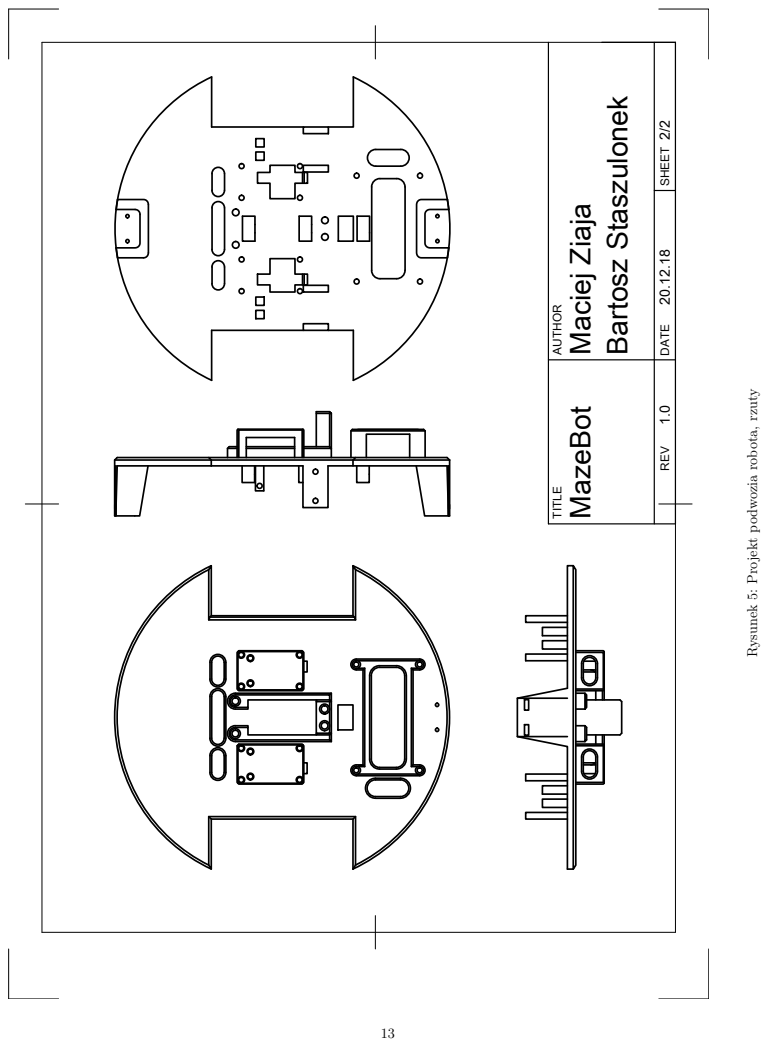
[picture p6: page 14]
TITLE; AUTHOR; MazeBot; Maciej Ziaja

Bartosz Staszulonek Rysunek 5: Projekt podwozia robota, rzuty

REV DATE SHEET

Syntezowany układ będzie miał na celu regulację prędkości silnika slave na podstawie odczytu prędkości silnika master. Dodatkowo silnik master będzie regulowany ze stałą wartością zadaną prędkości w celu zapewnienia większej pewności jego pracy. Regulator prędkości silnikam slave powinien być typu pid lub pi. Obecność członu całkującego jest wymagana aby osiągnąć odpowiedni astatyzm układu. Dzięki całkowaniu układ wyrówna nie tylko chwilową prędkość platformy, ale również sumaryczną przebytą przez robota drogę, co jest kluczowe aby utrzymać poprawny kierunek jazdy. Dodatkowo obliczenia związane z członem całkującym są w naszym przypadku proste, ponieważ odczyt z enkoderów charakter drogi przebytej przez robota, czyli całki z prędkości. Regulator prędkości silnika master może być typu proporcjonalnego. Zwiększanie astatyzmu tego silnika nie ma znaczenia dla jego poruszania się po lini prostej. W regulatorach nie zastosowano członu różniczkującego, który nie jest konieczny, a utrudniałby konstrukcję układów i sprawiał wyzwania obliczeniowe. Schemat 6 obrazuje konstrukcję planowanego układu regulacji prędkości silników. Układem zadajnika dla regulatora slave jest pomiar

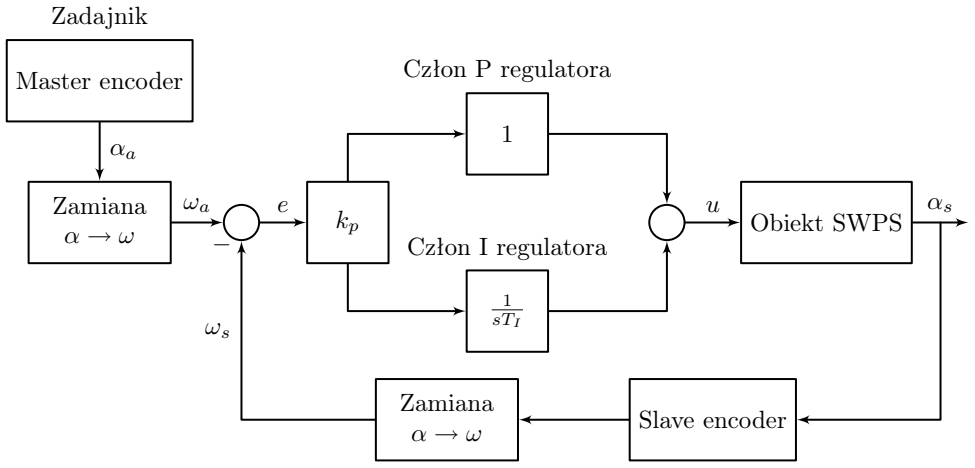
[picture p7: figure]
Master encoder; Zadajnik; Zamiana α → ω; Człon P regulatora; 1 sTI; Człon I regulatora; Obiekt SWPS; Slave encoder Zamiana α → ω

Rysunek 6: Wyjściowy schemat blokowy układu regulacji

pracy silnika master. Układ slave objęty jest pętlą sprzężenia zwrotnego z enkoderem szczelinowym w torze pomiarowym. Za regulację prędkości odpowiada układ typu pi Ilość zliczonych szczelin oznaczono na schemacie jako α, prędkość silników (ilość szczelin w czasie) oznaczono jako ω, silnik master oznaczono indeksem m, a silnik slave indeksem s. Jest to wyjściowy schemat regulatora, który nie jest dopasowany do charakteru toru pomiarowego i implementacji programistycznej.
Układ należy przekształcić w celu jego łatwiejszej implementacji. Czujniki szczelinowe zwracają do układu pomiar liczby szczelin na tarczy enkodera, co jest ekwiwalentem całki z prędkości, dlatego będziemy dążyć do usunięcia operacji całkowania z układu i bloku zamiana α na ω. W pierwszym kroku przekształceń układu skorzystamy z rozłączności operacji całkowania i przeniesiemy to działanie przed regulator oraz obliczymy całkę sygnału i wartości zadanej osobno, a uchyb wyznaczymy z różnicy tych całek. Układ po tym przekształceniu obrazuje schemat 7. W następnym kroku można zauważyć, że blok zamiana α na ω jest operacją różniczkowania, czyli mnożenia przez operator s. Wynika z tego że możemy skrócić bloki całkowania 1
s

i różniczkowania s. Finalny projekt układu regulacji przedstawia schemat 8. Tarcze enkoderów wprowadzają do układu dyskretyzację oraz błąd kwantyzacji. Silnik slave, który nadąża za silnikiem master zacznie się obracać po nim, a obrót od startu układu do pierwszej szczeliny silnika master sprawia, że w układzie pojawia się błąd. Błąd ten jest zależny od odległości punktu pomiarowego enkodera do pierwszej zliczonej szczeliny. Pozycja punktu pomiaru w momencie startu robota jest losowa, podobnie błąd z tego wynikający. Aby zmniejszyć ten problem do układu zdecydowano się dodać element sterowania w torze otwartym narzucający punkt pracy regulatorów. Dzięki temu w momencie startu oba silniki są wysterowane do jazdy na wprost. Wartości punktu pracy dla obu silników należy wyznaczyć eksperymentalnie, są one zależne od niesymetryczności charakterystyk silników.

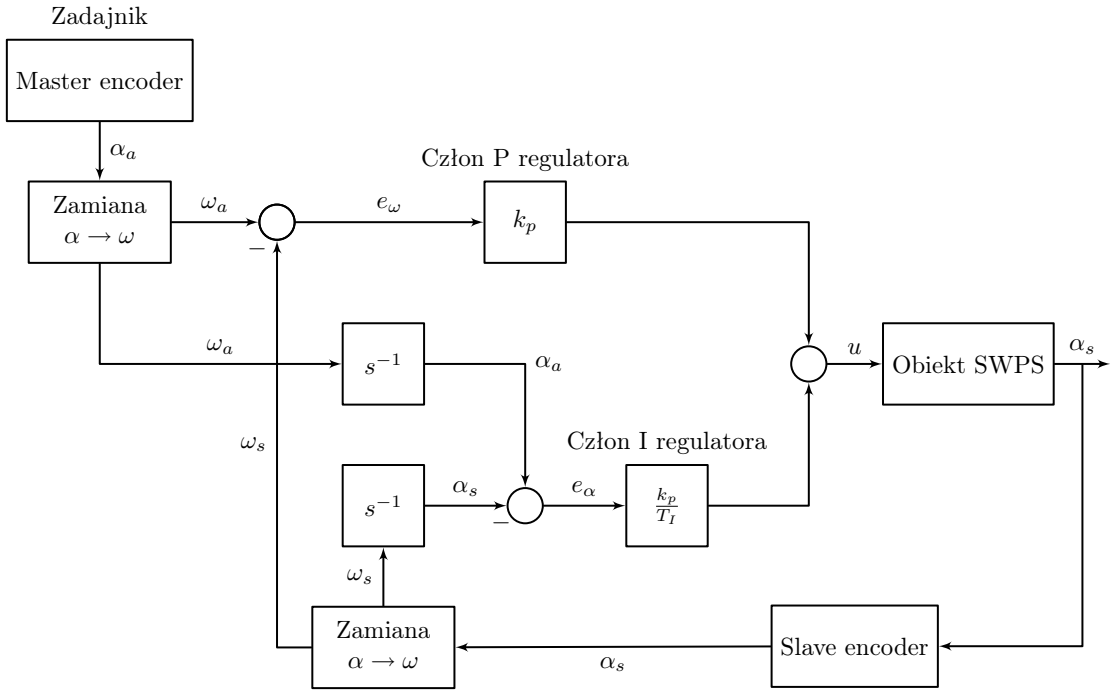
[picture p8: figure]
Master encoder; Zadajnik; Zamiana α → ω; Człon P regulatora; Człon I regulatora; Obiekt SWPS; Slave encoder

Rysunek 7: Schemat blokowy układu regulacji trakcie przekształceń

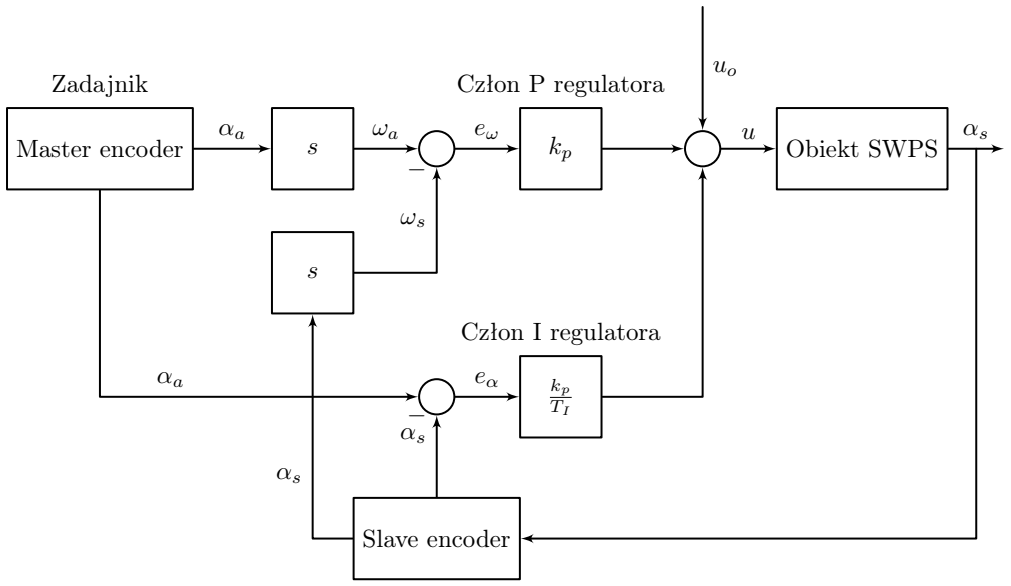
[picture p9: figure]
Master encoder; Zadajnik; Człon P regulatora; Człon; I regulatora; Obiekt SWPS; Slave encoder

Rysunek 8: Finalna konstrukcja układu regulacji

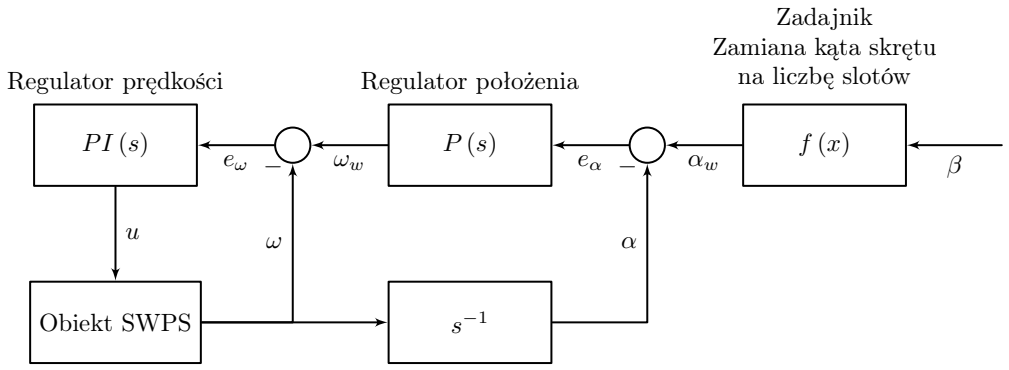
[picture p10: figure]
Zadajnik Zamiana kąta skrętu na liczbę slotów; Regulator położenia; Regulator prędkości; Obiekt SWPS

Rysunek 9: Schemat blokowy kaskadowego układu regulacji

### 6.2 Kaskadowy regulator skrętu platformy

Kolejnym problemem jest zapewnienie powtarzalności i precyzji obrotów platformy robota. W tym celu należy zbudować regulator położenia platformy, którego wartością zadaną jest ilość szczelin zliczona przez enkodery. Ilość szczelin potrzebna do obrotu platformy o zadany kąt jest zależna od konstrukcji mechanicznej robota, w sposób który wyraża wzór 2, gdzie:

- α to liczba slotów potrzebnych do obrotu o zadany kąt,
- β to zadany kąt obrotu całej platformy robota,
- αdisk to liczba szczelin na tarczy enkodera,
- wheelbase to rozstaw osi podwozia,
- dw to średnica kół.

α = round

β
360°
- 2 · αdisk ·

wheelbase
dw
(2)

Wzór wynika z proporcji obrotu koła do obrotu całej platformy robota wokół osi przebiegającej przez jej środek. We wzorze można zauważyć podwajanie liczby szczelin, wynika to z wyzwalania przerwania zliczania szczelin zarówno na zboczu rosnącym jak i malejącym w celu zwiększenia rozdzielczości pomiaru.
Jeżeli w układzie zastosujemy regulator proporcjonalny z pojedynczą pętlą sprzężenia zwrotnego napotkamy na problem szczególnie widoczny przy obrotach o mały kąt przy dużych oporach ruchu. Kiedy taki regulator wyznaczy wysterowanie silników, na podstawie uchybu ilości zliczonych szczelin, może się okazać że jest ono zbyt małe, aby poruszyć podwoziem silnika. Dodane do regulatora członu całkującego spowoduje, że po czasie kiedy wartość uchybu całki będzie odpowiednio duża układ ruszy z miejsca. Musimy jednak pamiętać, że układ regulacji położenia wpływa na obiekt o charakterze całkującym (bo ilość zliczonych slotów jest ekwiwalentem drogi). Regulacja z członem całkującym obiektów całkujących prowadzi do utworzenia niestabilnych układów regulacji. Rozwiązaniem tego problemu jest zastosowanie regulatora o strukturze kaskadowej, widocznego na rysunku 9. Regulator taki składa się z dwóch pętli sprzężenia, zewnętrznej i wewnętrznej oraz towarzyszących im regulatorów: odpowiednio położenia i prędkości. Regulator położenia ustala prędkość zadaną potrzebną do wykonania obrotu na podstawie uchybu liczby szczelin. Regulator prędkości otrzymuje swoją wartość zadaną od regulatora położenia. Regulator wewnętrzny, prędkości może zawierać człon całkujący, ponieważ nie reguluje samodzielnie układu całkującego. Ponieważ pokonanie oporu ruchów przy starcie jest trudniejsze od kontynuowania rozpoczętego obrotu[5] to zdecydowano się na odwijanie całkowania (zerowanie) przy każdej zliczonej szczelinie. Mogłoby to spowodować niepłynny ruch robota, natomiast sprawdzono eksperymentalnie, że obrane nastawy są wystarczające, aby człon proporcjonalny powodował płynny ruch obracającej się platformy, przy częstym zerowaniu członu całkującego. Powoduje to też łagodne zatrzymanie robota, co sprzyja eliminowaniu poślizgów i minimalizuje wybieg silnika i przeregulowania.

6.2.1 Wyznaczenie przedziału błędów w układzie.

Układ nie jest wolny od błędów związanych z jego konstrukcją mechaniczną i implementacją rozwiązań. Tarcza enkodera ze skończoną liczbą szczelin powoduje dyskretyzację działania układu i powstanie opóźnienia w synchronizacji silników master oraz slave. Ponieważ błąd ten ma charakter błędu kwantyzacji można go łatwo oszacować. Zgodnie z [4] błąd taki ma rozkład równomierny, jego skrajne wartości można wyliczyć według wzoru 3 gdzie:

- αdisk to liczba szczelin na tarczy enkodera,
- liczbę szczelin podwojono, ponieważ przerwanie wyzwalane jest na obu zboczach w celu zwiększenia rozdzielczości enkodera.

∆αmax = ±

360°

αdisk · 2

·

1
2
= ±4.5° | (3)

Ponieważ rozkład szumu kwantyzacji jest równomierny prawdopodobieństwo błędu o każdej wartości z tego przedziału wynosi 1
q

, gdzie: q =

360°
αdisk·2
. Należy również pamiętać, że pętla sprzężenia zwrotnego i pomiar enkoderów nie obejmują prawdziwego położenia platformy, a jedynie obroty koła. Wszelkie poślizgi powodują ruch który nie zostanie zarejestrowany przez enkodery. Należy pamiętać, że silniki mają wybieg, to znaczy nie zatrzymują się natychmiastowo po wyłączeniu sterowania. Duże wybiegi, przy dużych prędkościach będą powodować oscylacje w układzie skrętu o kąt zadany. Jest to niepożądane, nie tylko ze względu na niską jakość regulacji, ale komplikuje oprogramowanie układu, ponieważ enkodery nie mierzą w którą stronę kręcą się silniki, a jedynie zliczają kolejne impulsy. Dlatego przy strojeniu regulatora kluczowe jest aby dobrać nastawy gwarantujące brak oscylacji w układzie. Dodatkowo podczas programowania ograniczono wartość prędkości zadanej wypracowywanej w regulatorze kaskadowym przez regulator położenia. Zapobiega to zbyt gwałtownym startom platformy, z którymi mogłyby się wiązać niepożądane poślizgi.

### 6.3 Identyfikacja obiektu regulacji

W celu poprawnego strojenia regulatorów należy zbudować model obiektu regulacji. W naszym przypadku obiektami są silniki prądu stałego. Prostym sposobem identyfikacji obiektu jest podanie na jego wejście skoku jednostkowego i analiza uzyskanej odpowiedzi czasowej. Eksperyment identyfikacyjny wykonano podając skok w postaci wysterowania silników wartością pwm równą 100. Należy pamiętać, że z punktu widzenia układów regulacji, które utworzymy na odstawie identyfikacji, ta wartość wysterowania będzie równa jedności. Przy zadawaniu wartości silnikom sygnały będzie należało odpowiednio skalować. Odpowiedź czasową na wymuszenie jednostkowe otrzymano przez komunikację poprzez port szeregowy USB. Utworzono program testowy, który drukował przez port liczbę slotów i czas zliczeń. Dane przekazywano komputerowi w formacie zgodnym z csv (comma separated value), dzięki temu ich import do programu matlab mógł się odbyć w łatwy sposób. Program identyfikujący parametry obiektów na podstawie wyników eksperymentu przedstawia listing 1.
Odpowiedź układu zarejestrowano dla silników bez obciążenia i dla silników pod obciążeniem podwozia. Wyniki eksperymentu zobrazowano na wykresach. Rysunki 10(a) oraz 10(b) przedstawiają odpowiedzi silników bez obciążenia, rysunki 11(a), 11(b) przedstawiają odpowiedzi silników pod obciążeniem podwozia robota.
Ponieważ jako odpowiedź układu zliczano sloty, które są ekwiwalentem drogi należało spodziewać się odpowiedzi o charakterze całkującym. Wyniki identyfikacji potwierdziły te przypuszczenia, wykresy przypominają odpowiedź układu o transmitancji całki z inercją. Można zauważyć, że odpowiedzi silnika lewego i prawego różnią się, co potwierdza obserwacje dotyczącą ich niesymetrycznej pracy. Widać także, że przy obciążeniu silników podwoziem mają one większą bezwładność, czego również należało się spodziewać. Podczas strojenia układów regulacji należy bazować na parametrach obiektów identyfikowanych pod obciążeniem podwozia. Zaprojektowane układy mają na celu regulację prędkości, stąd odpowiedź należałoby zróżniczkować aby uzyskać odpowiedź prędkości w czasie. Nie jest to jednak konieczne, zróżniczkowanie odpowiedzi da wykres inercji pierwszego rzędu, z którego należy

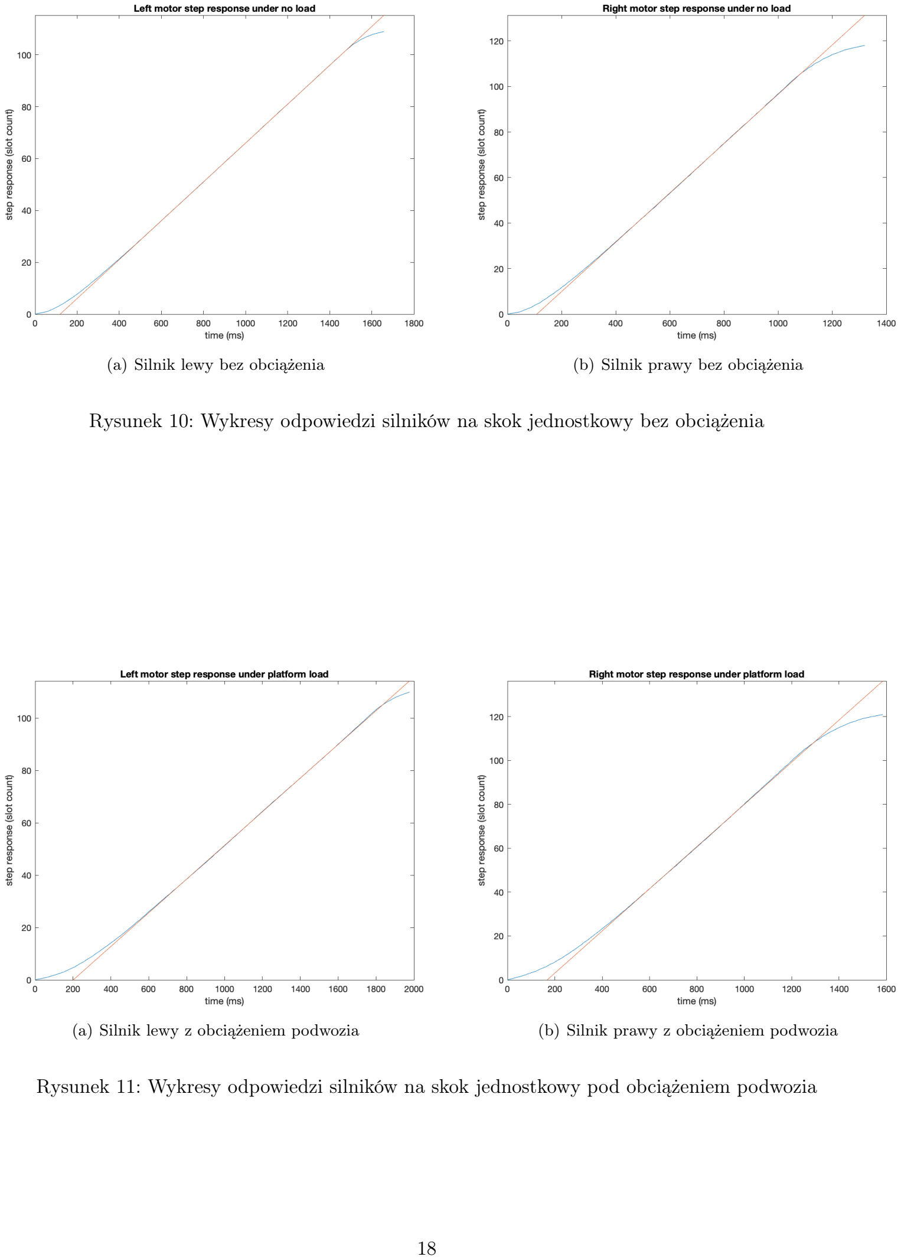
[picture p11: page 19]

(a) Silnik lewy bez obciążenia | (b) Silnik prawy bez obciążenia

Rysunek 10: Wykresy odpowiedzi silników na skok jednostkowy bez obciążenia

(a) Silnik lewy z obciążeniem podwozia | (b) Silnik prawy z obciążeniem podwozia

Rysunek 11: Wykresy odpowiedzi silników na skok jednostkowy pod obciążeniem podwozia

Listing 1: Identyfikacja parametrów transmitancji silników

function [kv, T] = motorIdentif(csv_name) % Plot step response.
figure()
objectResponse = csvread(csv_name); t = objectResponse(:, 1);
y = objectResponse(:, 2);
plot(t, y);
hold on;
% Fit line to the middle part of the step response. coeffs = polyfit(t(31:86), y(31:86), 1);
fittedX = linspace(min(t), max(t), 200);
fittedY = polyval(coeffs, fittedX);
% Plot fitted line.
plot(fittedX, fittedY);
hold off;
ylim([0 inf]);
xlabel('time (ms)');
ylabel('step response (slot count)');
% Calculate and return object transfer function parameters. T = -coeffs(1) / coeffs(2);
kv = coeffs(1);
end

odczytać stałą czasową i wzmocnienie układu. Te same parametry da się określić również z wykresu odpowiedzi drogi w czasie. W celu ich określenia należy wykreślić prostą do wykresu odpowiedzi. Punkt przecięcia prostej z osią x będzie określał stałą czasową układu, natomiast nachylenie prostej jego wzmocnienie. Ponieważ układ przybliżamy transmitancją całki z inercją, jego transmitancja będzie miała postać przedstawioną na wzorze 5. Parametry stałej czasowej T i wzmocnienia k, można obliczyć z dopasowanej do odpowiedzi prostej, według wzorów 4.

y(t) = a · t + b

k = a

T = −

a
b

(4)

Ko1 (s) = k s (1 + sT)
(5)

Identyfikacja układu i wykresy zostały wykonane w środowisku matlab, kod programu identyfikacyjnego przedstawia listing 1.

### 6.4 Strojenie regulatorów

Ponieważ regulatory PI będą regulowały prędkość silników należy przekształcić odpowiedź tak by uzyskać wykres prędkości w czasie. Uzyskana identyfikacja obiektu całkującego opisuje zmiany drogi w czasie, aby uzyskać transmitancję związaną ze zmianami prędkości należy zróżniczkować transmitancję obiektu całkującego przemnażając ją przez operator s, co obrazują przekształcenia we wzorze 6. Jak widać zmiany prędkości w czasie są opisane modelem inercyjnym.

Ko2 (s) = s · Ko1 (s) = s ·

k
| s (1 + sT)

=

k
1 + sT

(6)

Zdecydowano się na regulator PI, który ma wystarczający astatyzm, oraz jest łatwy w implementacji. W przypadku naszego układu, który opisujemy transmitancją niskiego rzędu odpowiednim sposobem strojenia będzie użycie lini pierwiastkowych. W celu wykreślenia linii najlepiej zapisać transmitancję regulatora i obiektu w postaci zero-biegunowej, którą przedstawia wzór 7.

P I (s) · Ko2 (s) =

s + c
s
·

k
1 + sT

(7)

Należy zdecydować o wartości dodanego zera c. Jego stosunek do stałej czasowej T zdecyduje o kształcie linii pierwiastkowych. Można rozpatrzeć trzy przypadki:

- zero większe do stałej czasowej: c > T,
- zero równe stałej czasowej: c = T
- zero mniejsze od stałej czasowej: c < T.

Przypadek równości tych parametrów jest najbardziej korzystny, doprowadzi do skrócenia fragmentów transmitancji, w takim wypadku regulator działałby jak korektor, a układ byłby najszybszym z możliwych. Mimo tego jest to przypadek, który należy odrzucić. Aby osiągnąć równość parametrów należałoby przeprowadzić identyfikację o nieosiągalnej dokładności, jednak wyznaczona wartość stałej czasowej może, i zapewne różni się od rzeczywistych parametrów układu. Mało prawdopodobne jest zrealizowanie korektora, a dobór zera równego zidentyfikowanej stałej czasowej da w rzeczywistości niespodziewane rezultaty, ze względu na niedoskonałości procesu identyfikacji. Należy rozpatrzyć pozostałe dwa przypadki, liniowe pierwiastkowe dla nich wykreślono na rysunkach 12(a) oraz 12(b). Program kreślącey linie pierwiastkowe w środowisku matlab, na podstawie identyfikacji obiektu przedstawia listing 2.

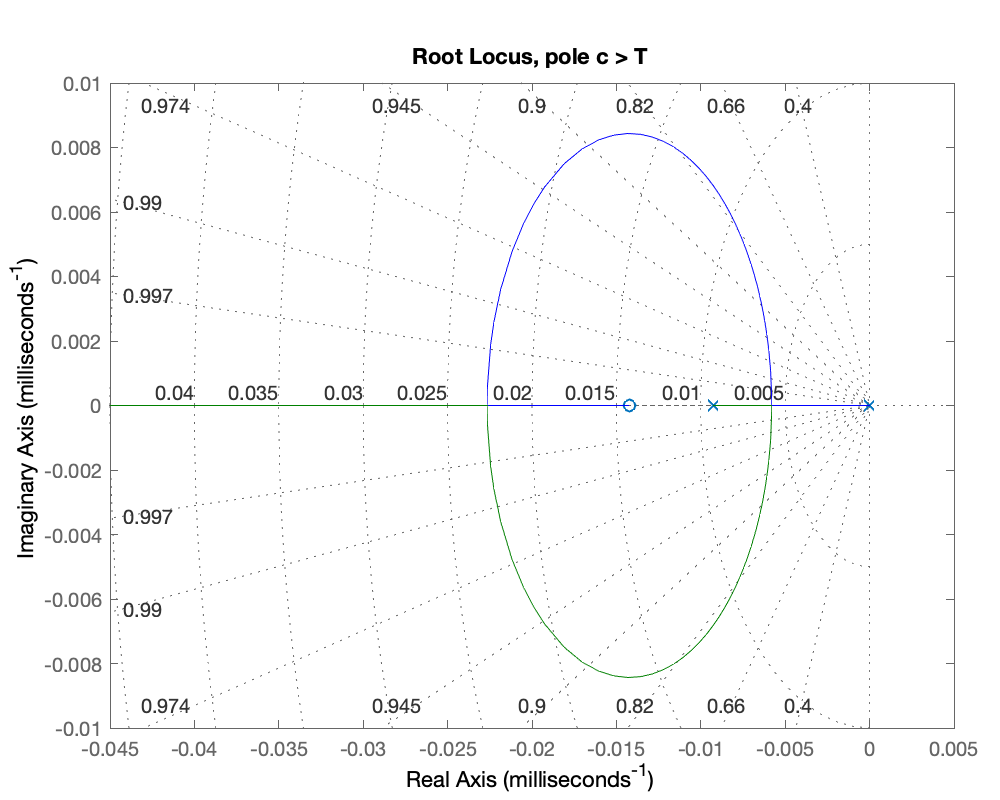
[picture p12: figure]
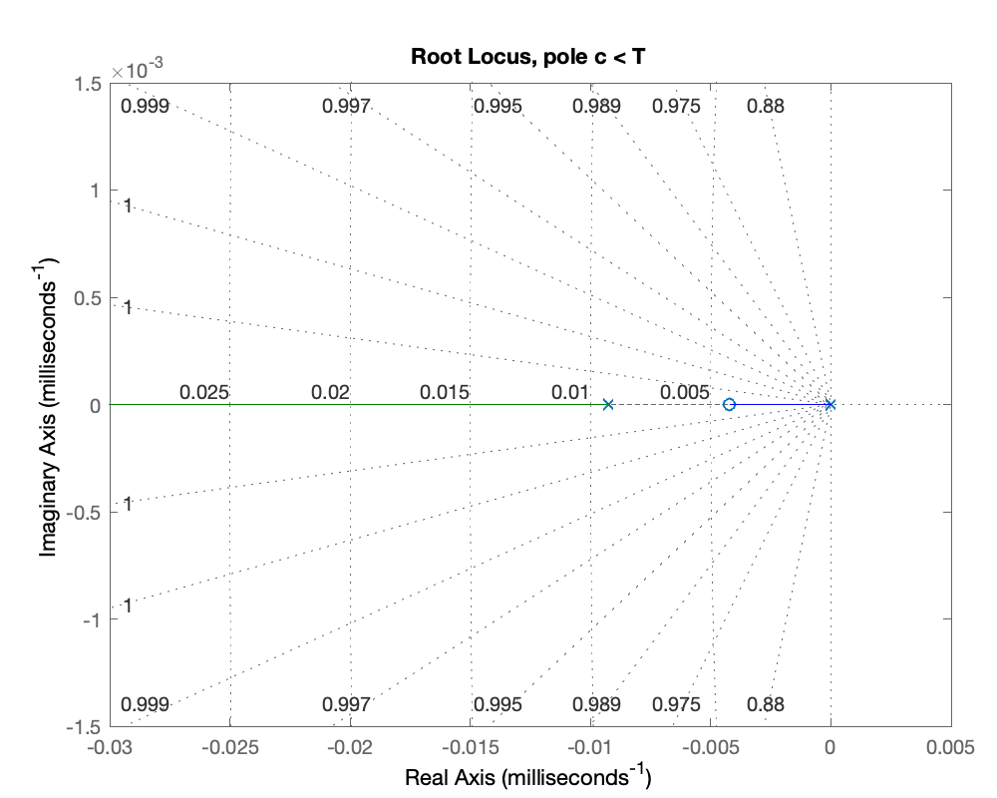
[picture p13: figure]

(a) Wariant z zerem większym od stałej czasowej | (b) Wariant z zerem mniejszym od stałej czasowej

Rysunek 12: Rozpatrywane linie pierwiastkowe układu z regulatorem pi

Prędkość działania finalnego układu jest zdeterminowana przez położenie bieguna, który znajduje się najbliżej osi urojonej y. Im bardziej od osi oddalony jest ten biegun tym szybszy układ. Przy analizie linii pierwiastkowych należy również pamiętać, że położenia biegunów o niezerowej części urojonej oznaczają oscylacje układu. Jak wspomniano w sekcji 6.2.1 zależy nam na konstrukcji układu aperiodycznego6
, czyli powinniśmy umieścić nasze bieguny na osi x. Można zauważyć że przypadek c > T pozwala na zbudowanie szybszego regulatora. W takiej konfiguracji, przy dużych wzmocnieniach najwolniejszy biegun znajduje się z lewej strony założonego zera, czyli dalej od osi urojonej y. W konfiguracji c < T najwolniejszy biegun znajduje się po prawej stronie

tzn. bez oscylacji.

Listing 2: Program kreślący linie pierwiastkowe układu na podstawie identyfikacji obiektu

% Get object parameters based on step response in csv file
% and print the response of each motor.
[kl, Tl] = motorIdentif('motorLeftIdentif.csv'); title('Left motor step response under no load');
[kll, Tll] = motorIdentif('motorLeftIdentifLoad.csv') title('Left motor step response under platform load'); [kr, Tr] = motorIdentif('motorRightIdentif.csv') title('Right motor step response under no load'); [krl, Trl] = motorIdentif('motorRightIdentifLoad.csv') title('Right motor step response under platform load');

% Plot root locus for right motor (which acts as slave). % First option for pole c < T
figure
s = tf('s');
motRight = kr / (s + Tr);
c = Tr - 0.005;
motRight = motRight * (s + c)/s; motRight.TimeUnit = 'milliseconds'; rlocus(motRight)
title('Root Locus, pole c < T');

% Second option for pole c > T figure
s = tf('s');
motRight = kr / (s + Tr);
c = Tr + 0.005;
motRight = motRight * (s + c)/s; motRight.TimeUnit = 'milliseconds'; rlocus(motRight)
title('Root Locus, pole c > T');

zera, czyli taki układ jest wolniejszy. Przypadek c > T zdaje się bardziej korzystny, jednak niesie ze sobą ryzyko oscylacji. Teoretycznie najlepsze położenie bieguna w tej konfiguracji to miejsce w którym pierwiastki wracają z koła wartości urojonych z powrotem na oś rzeczywistą x. Jest to jednak lokacja ryzykowna ze względu na niedoskonałości identyfikacji. Przez jej błędy możemy omyłkowo, w układzie rzeczywistym, ulokować bieguny z częścią urojoną, czyli wprowadzić oscylacje. Dla pewności wyeliminowania oscylacji należy zwiększyć wzmocnienie układu i umieścić pierwiastki dalej od koła wartości urojonych. Wadą takiego rozwiązania jest spowolnienie układu przez zbliżenie bieguna do osi y oraz wymaganie dużego wzmocnienia, które może być niemożliwe dla układu realizującego algorytm sterowania i elementów wykonawczych. Konfiguracja c < T może być praktycznie lepsza, niż mogło zdawać się pierwotnie, nie niesie ryzyka oscylacji. Fakt, że taka konfiguracja jest wolniejsza niesie pewne zalety, mało gwałtowne ruchy robota minimalizują ryzyko poślizgów kół. W celu nastrojenia układów regulacji należy wykonać eksperymenty i porównać oczekiwania wynikające z linii pierwiastkowych z rzeczywistością.

### 7 Implementacja programistyczna

### 7.1 Podział i organizacja kodu

Kod odpowiadający za różne funkcjonalności robota umieszczono w oddzielnych plikach, w których znajdują się funkcje budujące warstwy abstrakcji peryferiów konstrukcji. Zdecydowano się na następujący podział plików i funkcji:

- defines zawiera stałe programu oraz makroinstrukcje,
- servoSensor zawiera funkcje budujące warstwę abstrakcji czujnika ultradźwiękowego na wieży serwomechanizmu, pozwala na kierowanie czujnika w różne strony, wykrywanie przeszkód oraz poszukiwanie wolnej drogi w otoczeniu,
- platformMotors zawiera funkcje budujące warstwę abstrakcji platformy robota, pozwala na jazdę na wprost oraz skręty, bazuje w działaniu na układach regulacji,
- HC_SR04 zawiera zmodyfikowaną bibliotekę obsługi czujnika ultradźwiękowego w trybie nieblokującym, biblioteka jest wykorzystywana przez funkcje z pliku servoSensor,
- main zawiera główną logikę programu, wywołuje funkcje poszukiwań drogi bez przeszkód i podążania w tym kierunku, kontroluje także wyłączanie i włączanie układu po odebraniu rozkazów wysłanych podczerwienią.

### 7.2 Algorytm omijania przeszkód

Kluczowym elementem omijania przeszkód jest znajdywanie drogi, na której nie znajdują się przeszkody. Proces znajdywania nowego kierunku jazdy rozpoczyna się w momencie, w którym na obecnym kierunku jazdy zostaje wykryta przeszkoda. Wtedy robot się zatrzymuje i losuje po której stronie najpierw będzie szukał wolnej drogi. Potem zwraca w tym kierunku czujnik ultradźwiękowy i wykrywa obecność przeszkód. Jeżeli te nie zostaną wykryte platforma skręca w wylosowanym kierunku i rozpoczyna jazdę na wprost. W przeciwnym przypadku robot kieruje czujnik w przeciwną stronę i bada czy tam znajduje się przeszkoda, jeżeli nie to rozpocznie jazdę w tym kierunku. Kiedy obie strony robota są zablokowane ten zwróci się w kierunku z którego przyjechał. Opisane zachowanie obrazuje schemat na rysunku 13.

### 7.3 Algorytmy regulacji

### 7.3.1 Algorytm regulacji synchronizacji prędkości silników

Algorytm synchronizacji został zaprogramowany według schematu na rysunku 13. Kod realizujący założenia schematu przedstawiono na listingu 3. Parametry regulatora należy przekształcić względem tych uzyskanych z analizy linii pierwiastkowych, aby ułatwić obliczenia i czytelność kodu. Formuła regulatora zastosowana w kodzie ma postać jak we wzorze 9, gdzie:

- ∆α to uchyb ilości zliczonych slotów,
- ∆ω to uchyb chwilowej prędkości,

Parametry regulatora w takiej postaci można wyliczyć według wzoru 8, gdzie:

- kr to wzmocnienie regulatora odczytane z linii pierwiastkowych,
- c to wartość zera transmitacnji ze wzoru 7.

P = kr
I = kr · c

(8)

P I (∆α, ∆ω) = P · ∆α + I · ∆ω | (9)

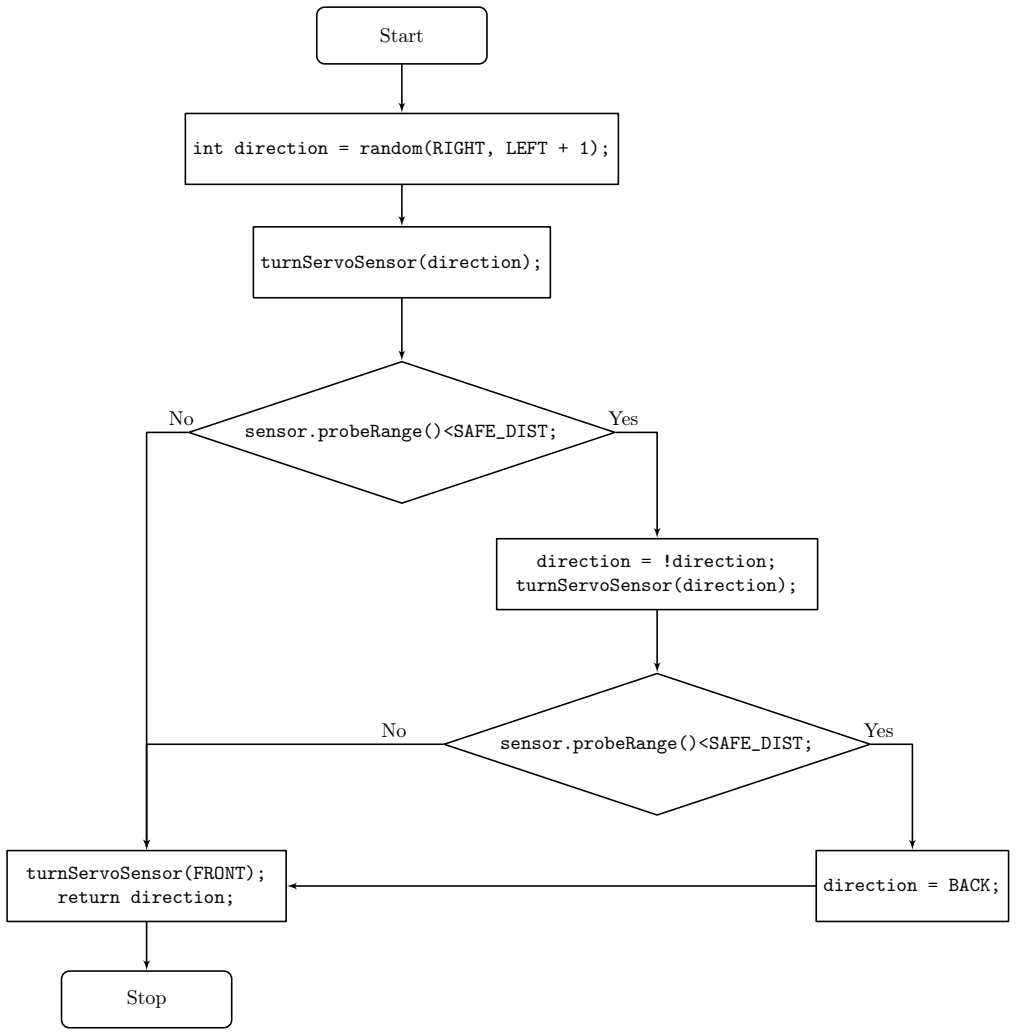
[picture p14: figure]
Start; turnServoSensor(direction);; sensor.probeRange()<SAFE_DIST;; direction = !direction; turnServoSensor(direction);; direction = BACK; turnServoSensor(FRONT);; return direction;; Stop; Yes

int direction = random(RIGHT, LEFT + 1);

Rysunek 13: Schemat blokowy algorytmu znajdywania kierunku bez przeszkód

Listing 3: Algorytm regulacji synchronizacji prędkości silników

164 | void headingVeloFix() {
165 | int actuationLeft; | ///< Actuation of the left motor, steers the motor's PWM.
166 | int actuationRight; ///< Actuation of the right motor, steers the motor's
,→ | PWM.

167
168 | float Pm = 10; | ///< Proportional coefficient of master velocity
,→ | controller.
169 | float Ps = 15; | ///< Proportional coefficient of slave velocity
,→ | controller.
170 | float Is = 5; | ///< Integral coefficient of slave velocity controller.

171
172 | /* Master controller */
173 | float veloDeltaLeft = ((float)200.0/20.0) - (200.0/((float)
,→ | motLeftDeltaTime));
174 | actuationLeft = 112 + round(Pm * veloDeltaLeft);
175 | if(actuationLeft > 255) actuationLeft = 255;

176
177 | /* Slave controller */
178 | float veloDelta = ((200.0/((float) motLeftDeltaTime)) - (200.0/((float)
,→ | motRightDeltaTime)));
179 | int slotDelta = motLeftCounter - motRightCounter;
180 | actuationRight = 88 + round(Ps * veloDelta + Is * slotDelta);
181 | if(actuationRight > 255) actuationRight = 255;

182
183 | /* Actuate motors */
184 | motorRotateRight(actuationRight);
185 | motorRotateLeft(actuationLeft);

186
187 | #if HEADING_VELO_FIX_DBG
188 | PRINT_HEADING_VELO_FIX_DBG
189 | #endif
190 | }

### 7.3.2 Algorytm regulacji skrętu o kąt zadany

Algorytm regulacji skrętu o kąt zadany został zaprogramowany według schematu na rysunku 9. Kod pętli wewnątrz której realizowana jest regulacja przedstawiony jest na listingu 4. Wypracowanie sterowania rozpoczyna się od wyznaczenia uchybu ilości slotów wymaganych do wykonania obrotów. Wartość zadana target regulatora położenia jest wyliczana z makrofunkcji realizującej wzór 2. Wartość zadana prędkości została ograniczona, aby zapobiec poślizgom. Wartość zadana regulatora prędkości jest wypracowywana przez regulator położenia. Różniczkowanie ilości slotów w celu otrzymania prędkości chwilowej zrealizowano przez odwracanie czasu zliczonego między ostatnimi przerwaniami wygenerowanymi przez czujniki szczelinowe. Kod przerwań czujników przedstawia listing 5 Istotne jest aby pamiętać o rzutowaniu wartości int na float przy dzieleniu, aby zachować precyzję obliczeń. Całkowanie uchybu odbywa się przez mnożenie go przez czas jaki upłynął od ostatniego przerwania czujnika szczelinowego. W rozdziale 6.2 opisującym założenia budowy regulatora kaskadowego przedstawiono pomysł konstrukcji zerującej wartość całki przy każdym przerwaniu czujnika szczelinowego. Odpowiednikiem tego założenia w kodzie jest brak zapamiętywania i sumowania poprzednich wartości całki, przy każdej nowej szczelinie czas od tego przerwania jest liczony od nowa. Jest to bardzo uproszczona realizacja członu całkującego, jednak zupełnie wystarczająca w naszym przypadku7

### 7.4 Kod funkcji obsługującej przerwanie czujnika szczelinowego

Kod funkcji obsługującej przerwanie czujnika szczelinowego8 przedstawiono na listingu 5. Funkcje obsługi przerwań czujników szczelinowych mają za zadanie inkrementację licznika szczelin oraz obliczenie czasu od ostatniego przerwania. W funkcji należało uwzględnić inne zachowanie przerwań przy początku ruchu robota. Przy testach czujników okazało się, że przy zmianie stanu czujnika następuje zjawisko podobne do odbijania styków, co sprawiało że fałszywie zliczana była duża ilość szczelin. Aby temu zapobiec ignorowane są sygnały które pojawiły się zbyt szybko względem ostatniej zmiany. Tworząc kod przerwań należy pamiętać, że ich obsługa w mikrokontrolerach ATmega wyłącza działanie liczników, przez co funkcje millis() w przerwaniach zwracają czas włączenia przerwania, a czas który upłynął na obsłudze przerwania jest pomijany przy następnych wywołaniach funkcji millis(). To zjawisko mogłoby powodować błędy jeżeli zależałoby nam na precyzyjnym zliczaniu czasu od wydarzenia, kiedy podczas zliczania obsługujemy dużo przerwań o długim kodzie obsługi. Taka potrzeba nie zachodzi jednak w naszym przypadku, więc użycie funkcji millis() w kodzie obsługi przerwań jest bezpieczne.

### 8 Wykorzystane technologie

### 8.1 Narzędzia programistyczne

Ze względu na ograniczenia programu Arduino IDE zdecydowano się na użycie środowiska PlatformIO9 ,
które jest wtyczką do programu Visual Studio Code10. Taka konfiguracja oferuje:
- bogate kolorowanie składni języków programowania,
- zaawansowany system autouzupełniania kodu z użyciem technologii IntelliSense,
- automatyczne wykrywanie portów szeregowych z podłączonymi płytkami,
- konstrukcja bazująca na plikach make i programie avrdude.

Kod projektu wersjonowano z użyciem programu Git oraz korzystając z usług serwisu GitHub, który oferuje internetowy interfejs do zarządzania repozytorium, system issue tracking oraz zarządzanie projektem za pomocą tablic kanban.

### 8.2 Komunikacja z mikroprocesorem

Do komunikacji z mikroprocesorem przydatny okazał się program avrdude. Szczególnie jego polecenia testu poprawnej komunikacji i odczytu fuse bitów. Poniżej przedstawiono przykład użycia polecenia testu mikrokontrolera oraz jego wynik:

$ sudo avrdude -p m32u4 -c usbasp -P usb
avrdude: AVR device initialized and ready to accept instructions
Reading | ############################################### | 100% 0.01s
avrdude: Device signature = 0x1e9587

7 Działanie członu całkującego można sprawdzić w sposób eksperymentalny. W tym celu wyłączono człon proporcjonalny, zerując jego parametr P. Robot powinien na początku nie ruszyć, a wraz z brakiem jego ruchu powinien być całkowany coraz większy uchyb i zadawane coraz większe wysterowanie silników. Po chwili powinien być słyszany odgłos silników próbujących pokonać opory ruchu. Ostatecznie wartość całki powinna być na tyle duża, że silniki ruszą i nastąpi obrót kół o kąt powodujący zliczenie jednej szczeliny. Ponieważ całkę zerujemy przy każdej zliczonej szczelinie, robot się zatrzyma i zacznie całkować uchyb od nowa. Proces ten będzie powtarzał się aż robot wykona stopniowo pełen skręt. Przewidywania te potwierdził eksperyment.
8Funkcje obsługi przerwań lewego i prawego czujnika należało napisać oddzielnie, ale ich kod jest praktycznie taki sam. Opisano tu kod obsługi jednego czujnika, ale drugi różni się tylko operacjami na innych zmiennych globalnych, logika jego działania jest identyczna.
9PlatformIO: https://platformio.org
10Visual Studio Code: https://code.visualstudio.com avrdude: safemode: Fuses OK
avrdude done. Thank you.

Polecenie odczytu fusebitów ma z kolei następujący format i daje wynik:

$ sudo avrdude -p m32u4 -c usbasp -P usb -U hfuse:r:hfuse.hex:h avrdude: AVR device initialized and ready to accept instructions
Reading | ############################################### | 100% 0.01s
avrdude: Device signature = 0x1e9587
avrdude: reading hfuse memory:
Reading | ############################################### | 100% 0.00s
avrdude: writing output file "hfuse.hex"
avrdude: safemode: Fuses OK
avrdude done. Thank you.

Jak widać w powyższych instrukcjach, do programowania mikrokontrolera użyto programatora USBasp. Przy zakupie takiego programatora warto upewnić się, że kupujemy wersję z najnowszym firmwarem, dzięki czemu programator będzie miał od razu dostępną funkcję automatycznego dopasowania do taktowania zegara mikrokontrolera. Program Arduino IDE pozwala na wypalenie w pamięci mikrokontrolera bootloadera Arduino. Opcja ta jest dostępna w pasku menu w zakładce narzędzia.

### 9 Perspektywy rozwoju, podsumowanie

Wykonany projekt spełnił założenia, dzięki zastosowaniu układów regulacji napędu silników robot jest stanie poruszać się na tyle precyzyjnie by wymijać przeszkody. Wszystkie elementy układu oraz części obwodu drukowanego działają w sposób poprawny. Załączniki do dokumentacji zawierają materiały multimedialne prezentujące osiągniętą dokładność pracy robota. Projekt miał charakter edukacyjny, jego wyników nie da się porównać z produktami komercyjnymi, jednak zdobyte podczas jego realizacji doświadczenie i fragmenty pracy mogą być przydatne przy konstrukcji robotów magazynowych, robotów labiryntowych oraz przy budowie dedykowanych serwomechanizmów.
Precyzję układu można zwiększyć stosując tarcze enkoderów o większej ilości szczelin, lub stosując enkodery umieszczane przed przekładnią silników. Ciekawą ścieżką rozwoju może być zamiana układu pomiarowego z enkodera badającego obroty kół na system Yaw, Pitch Roll. Jest to zestaw współpracujących ze sobą: żyroskopu, akcelerometru oraz magnetometru w celu ustalenia kierunku układu w przestrzeni poprzez kąty Eulera. Taki układ pomiarowy cechowałby się daleko większą dokładnością i obejmowałby pętlą sprzężenia zwrotnego nie tylko obroty silnika, ale rzeczywisty kierunek robota, eliminując błędy związane z poślizgiem kół. Na obecnym etapie projektu taki system pomiarowy znacząco przekroczyłby budżet, jednak w przyszłości może on stanowić ciekawe zagadnienie. Jego wprowadzenie pozwoliłoby na zachowanie sporej ilości aktualnego kodu, zmiany wymagałby jedynie tor pomiarowy i zadajnik.
Na bieżącym etapie układ nie zapamiętuje ścieżki którą przebył, aby to zmienić można skonstruować drzewo binarne wykonanych skrętów i odległości między nimi. Dzięki temu układ mógłby analizować przebytą drogę i szukać wyjścia z bardziej złożonych labiryntów. Kod programu, pliki Autodesk Eagle oraz dokumentacja są dostępne na stronie GitHub projektu: https://github.com/MaciejZj/MazeBot.

### Literatura

[1] Rafał Baranowski, Mikrokontrolery AVR ATmega w praktyce Wydawnictwo BTC, Warszawa 2005
[2] Stefan Węgrzyn, Podstawy automatyki Państwowe Wydawnictwo Naukowe, Warszawa 1974.
[3] Y. Takashi, M.J. Rabins, D.M. Auslander, STEROWANIE i systemy dynamiczne, Wydawnictwo Naukowo Techniczne, Warszawa 1976.
[4] Praca zbiorowa pod redakcją Dariusza Buchczika i Stanisława Walusia, Laboratorium Podstaw Miernictwa, Wydawnictwo Politechniki Śląskiej, Gliwice 2014.

[5] David Halliday, Robert Resnick, Jearl Walker, Podstawy Fizyki. Tom 1, Wydawnictwo Naukowe PWN, Warszawa 2003.
[6] Atmel: | ATmega16U4/ATmega32U4 | 8-bit | Microcontroller | with | 16/32K | bytes | of ISP
Flash | and | USB | Controller, | http://ww1.microchip.com/downloads/en/devicedoc/
atmel-7766-8-bit-avr-atmega16u4-32u4_datasheet.pdf (http://ww1.microchip.com/downloads/en/devicedoc/atmel-7766-8-bit-avr-atmega16u4-32u4_datasheet.pdf)
[7] STMicroelectronics: L298 DUAL FULL-BRIDGE DRIVER, https://www.sparkfun.com/datasheets/Robotics/L298_H_Bridge.pdf (https://www.sparkfun.com/datasheets/Robotics/L298_H_Bridge.pdf)
[8] Elec: | Ultrasonic | Ranging | Module | HC | - | SR04, | https://www.mouser.com/ds/2/813/
HCSR04-1022824.pdf (https://www.mouser.com/ds/2/813/HCSR04-1022824.pdf)
[9] Vishay: TSOP48 Photo Modules for PCM Remote Control Systems, http://mkpochtoi.narod.ru/TSOP4836_ds.pdf (http://mkpochtoi.narod.ru/TSOP4836_ds.pdf)
[10] STMicroelectronics: TL7800 series positive voltage regulators, https://datasheet.octopart.com/L7805CV-STMicroelectronics-datasheet-7264666.pdf (https://datasheet.octopart.com/L7805CV-STMicroelectronics-datasheet-7264666.pdf)
[11] Praca zbiorowa pod redakcją Krzysztofa Zioło LABORATORIUM ELEKTRONIKI I Elementy półprzewodnikowe i układy podstawowe. Wydanie III zmienione . Wydawnictwo Politechniki Śląskiej, Gliwice 1999.

Listing 4: Algorytm regulacji skrętu o kąt zadany

while(1) {
86 | int slotDeltaRight = target - motRightCounter; | ///< Error of position (precedent)
,→ | controller for right motor.
87 | int slotDeltaLeft = target - motLeftCounter; | ///< Error of position (precedent)
,→ | controller for left motor.

/* P regualtor formula, calcualtes velocity setpoint */
| setPointVeloRight = Pp * slotDeltaRight;
| setPointVeloLeft = Pp * slotDeltaLeft;

/* Avoid too high velocity set points to elude wheel slips during long turns */ if(setPointVeloRight > 16) setPointVeloRight = 16;
| if(setPointVeloLeft > 16) setPointVeloLeft = 16;
| /* Calulate velocity errors */
float veloDeltaRight = setPointVeloRight - (1.0/((float) motRightDeltaTime)); float veloDeltaLeft = setPointVeloLeft - (1.0/((float) motLeftDeltaTime));
/* Get current time to compare it with last time of ISR and estimate integral */
| unsigned long compareTime = millis();

/* PI controller formula, calculates motors actuations */
actuationRight = round(Pv * veloDeltaRight + Iv * veloDeltaRight * (compareTime -,→ lastTimeRight));
actuationLeft = round(Pv * veloDeltaLeft + Iv * veloDeltaLeft * (compareTime -
,→ | lastTimeLeft));
| /* Prevent oversaturation of PWM */
| if (actuationRight > 255) actuationRight = 255;
| if (actuationLeft > 255) actuationLeft = 255;

/* If target is reached stop the motor, otherwise actuate it */
| if (motLeftCounter >= target) {
| motorLeftStop(); leftIsStopped = true;
| } else
motorRotateLeft(direction * actuationLeft);
| if (motRightCounter >= target) {
| motorRightStop(); rightIsStopped = true;
| } else
motorRotateRight(-direction * actuationRight);
| #if TURN_ANGLE_DBG
| PRINT_TURN_ANGLE_DBG
| #endif /* If both motors are stopped exit function */
| if(leftIsStopped && rightIsStopped) {
| delay(MOTOR_STOP_DELAY);
| return; }

}

Listing 5: Kod funkcji obsługującej przerwanie czujnika szczelinowego

void motorLeftCounterInt() { /* When ISR is entered first time in the movement we shouldn't calculate time
| ,→ | delta */
if(motLeftCounter == 0) {
| | lastTimeLeft = millis(); motLeftCounter++; return;

}

/** Straightforward low pass filter, debounces the slot sensor
201 | * | when it is on the edge of a slot.
| */
unsigned long timeNow = millis();
if(timeNow - lastTimeLeft < 2) return;

/** Increment slot counter and calculate time delta to provide
207 | * | information for velocity calculation
| */
motLeftCounter++;
motLeftDeltaTime = timeNow - lastTimeLeft;

lastTimeLeft = timeNow;

}

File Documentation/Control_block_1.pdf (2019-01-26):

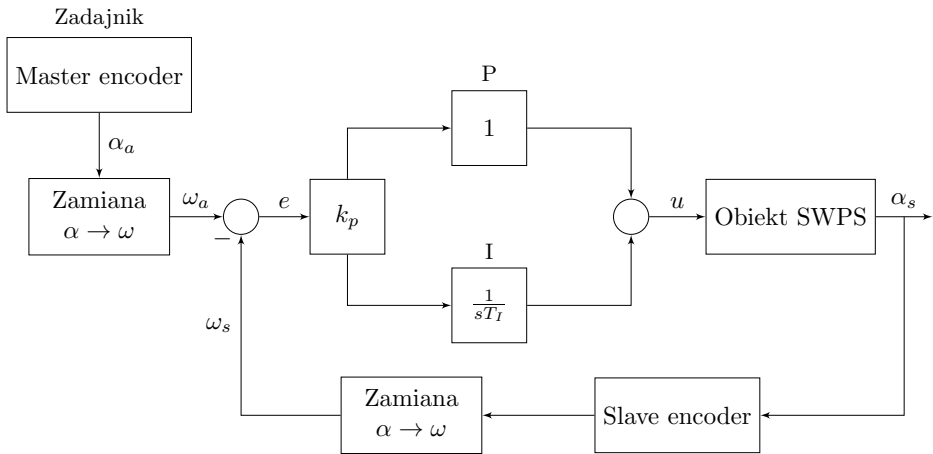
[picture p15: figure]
Master encoder; Zadajnik; Zamiana α → ω; 1 sTI; Obiekt SWPS u; Slave encoder Zamiana α → ω

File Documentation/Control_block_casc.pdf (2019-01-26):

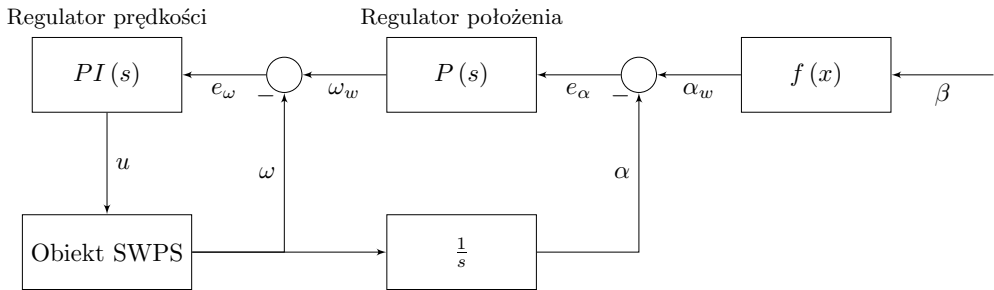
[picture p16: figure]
Regulator położenia; Regulator prędkości; Obiekt SWPS

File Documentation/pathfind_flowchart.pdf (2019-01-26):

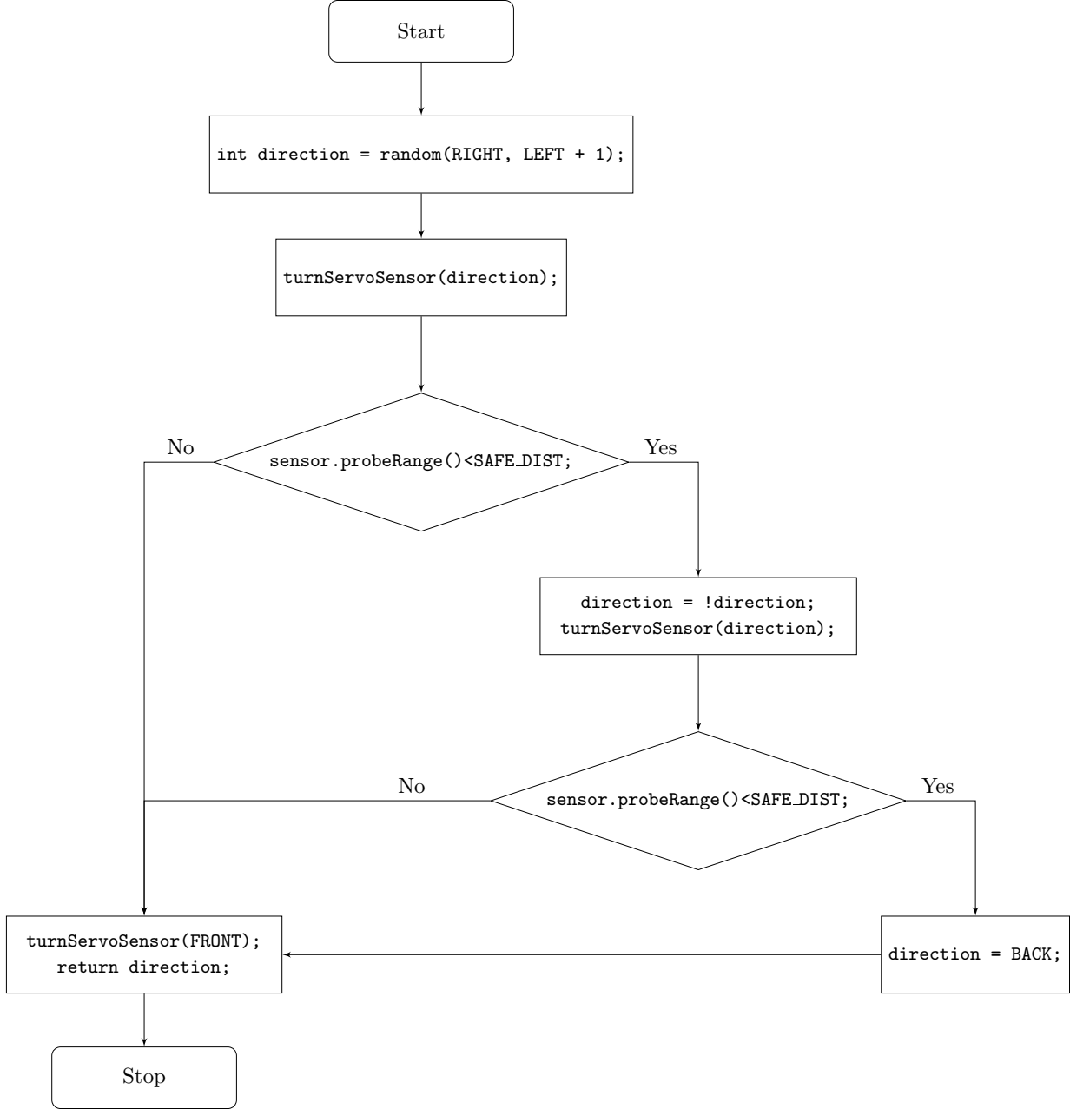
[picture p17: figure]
Start; turnServoSensor(direction);; sensor.probeRange()<SAFE DIST;; direction = !direction; turnServoSensor(direction);; direction = BACK;; turnServoSensor(FRONT); return direction;; Stop; Yes

int direction = random(RIGHT, LEFT + 1);

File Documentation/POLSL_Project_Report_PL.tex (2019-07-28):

\documentclass[11pt]{article}
\usepackage{polski}
\usepackage[utf8]{inputenc}
\usepackage[a4paper, margin=20mm]{geometry}
\usepackage{amsmath}                        % Math symbols
\usepackage{amssymb}                        % More math symbols
\usepackage{graphicx}                       % Figures, images
\usepackage{subfigure}                      % Multiple figures in one
\usepackage{footnote}                       % Footnote on bottom of page
\usepackage{rotating}                       % Rotate figures by given angle
\usepackage{slantsc}                        % Small caps
\usepackage[hidelinks]{hyperref}            % Hyperlinks without red box
\usepackage{standalone}                     % import standalone docs
                                            % Mainly for tikz
\usepackage[T1]{fontenc}                    % Best text enocoding
\usepackage[newfloat]{minted}               % For code listings
\usepackage{listings}
\renewcommand*{\listlistingname}{Spis listingów}
\setminted{autogobble}                      % Remove unnecessary indents
\usepackage{siunitx}                        % SI Units
\DeclareSIUnit \amperehour { Ah }
\DeclareSIUnit \mil { mil }

\usepackage{tikz}                           % Graphing and plotting
\usetikzlibrary{shapes,                     % Tikz common shapes
				arrows}                     % Tikz common arrows
\tikzstyle{every node}=[font=\small]        % Make tikz globally prettier
\tikzstyle{every path}=[line width=0.8pt,
						line cap=round,
						line join=round]

\graphicspath{ {Graphics/} }
\author{Maciej Ziaja}
\date{2 lutego 2019}

\begin{document}

\pagenumbering{gobble}
\title{
	Projekt Systemy Mikroprocesorowe \\
	\large MazeBot \\
	Robot unikający przeszkód z regulacją napędu silników prądu stałego}

\maketitle

\vfill
\begin{figure}[!htbp]
	\centering
	
\end{figure}
\vfill

\begin{sidewaysfigure}[!htbp]
	\centering
	
\end{sidewaysfigure}

\newpage
\pagenumbering{arabic}
\tableofcontents

\section{Wstęp}

\subsection{Abstrakt}
Projekt polega na konstrukcji mobilnego robota, który unika przeszkód.
Układ porusza się na dwóch kołach oraz wykrywa elementy otoczenia używając czujnika ultradźwiękowego zamocowanego na~wieży serwomechanizmu.
Platforma robota napędzana jest za pomocą pary silników prądu stałego, których kąt obrotu jest odczytywany przez czujniki szczelinowe.
W celu zwiększenia precyzji działania konstrukcji zbudowano układy regulacji prędkości silników.
Wykonano dwa typy układów regulacji: synchronizujący prędkość obrotu obu silników, w~celu zachowania kierunku jazdy na~wprost, oraz kaskadowy układ regulacji skrętu platformy robota.
Układ regulacji skrętu robota przypomina zasadą działania prosty serwomechanizm.
Przedstawiono metodę identyfikacji obiektu regulacji i~strojenia regulatorów z~użyciem linii pierwiastkowych.
Na potrzeby projektu wykonano także schemat układu elektronicznego i~zrealizowano go~w~postaci obwodu drukowanego \textsc{pcb}.
Zaprojektowano także podwozie robota i~wydrukowano je~w~technologii~3D.

\subsection{Cel i zakres projektu}
Projekt obejmował budowę platformy bazującej na~mikroprocesorze z~serii ATmega32, obsługującym peryferia:
\begin{itemize}
	\item czujnika ultradźwiękowego wykrywającego przeszkody,
	\item wieży serwomechanizmu, na której zamontowany jest czujnik i~która kieruje go w~różne strony,
	\item silników prądu stałego stanowiących napęd platformy,
	\item czujników szczelinowych odczytujących kąt obrotu kół platformy,
	\item odbiornika podczerwieni pozwalającego na~zdalne wyłączenie robota, jeśli ten się oddali.
\end{itemize}
Współpraca wymienionych komponentów pozwala robotowi na unikanie przeszkód.
Działanie robota powinno polegać na~jeździe przed siebie, do~czasu napotkania przeszkody.
W~momencie wykrycia przeszkody robot powinien się zatrzymać, a~następnie zbadać czy w~jego otoczeniu znajduje się niezagrodzona droga i~skierować się w jej stronę.
Prototyp układu wykonano z~użyciem układu Arduino Leonardo.
Na wykonanym prototypie wykonano testy współpracy komponentów i~wyciągnięto wnioski dotyczące budowy finalnej konstrukcji oraz wymaganych parametrów komponentów.
Działanie prototypu prowadziło do następujących decyzji projektowych, które podyktowały dalszy tok projektu i~jego zakres:
\begin{itemize}
	\item w~celu wydajnego wykorzystania przestrzeni na platformie zdecydowano się na wykonanie własnego układu elektronicznego i~obwodu drukowanego,
	\item zaprojektowano własne podwozie dopasowane do~używanych peryferiów,
	\item wykonano układy regulacji jazdy na wprost oraz skręcania platformy.
\end{itemize}

\section{Organizacja projektu}
\subsection{Harmonogram}
Projekt należało zrealizować w przeciągu 4 miesięcy.
Proces jego wykonania składał się z~dwóch części: testów komponentów wraz z~budową prototypu oraz konstrukcji finalnego układu, na~podstawie wniosków wyciągniętych z~testów konstrukcji prototypowej.
	Tabela \ref{tab:sched} przedstawia ramowy rozkład pracy w~czasie.

\begin{table}[hbt]
	\centering
	\begin{tabular}{|c|c|}
	\hline
Termin                  & Zakres pracy                                                                         \\ \hline
01.10.2018 - 20.10.2018 & Zebranie komponentów układu, ustalenie zakresu prac                                  \\ \hline
20.10.2018 - 01.11.2018 & Test komponentów i~peryferiów z użyciem Arduino Leonardo                             \\ \hline
01.11.2018 - 14.11.2018 & Budowa prototypu, programowanie głównej logiki programu \\ \hline
14.11.2018 - 01.12.2018 & Projekty obwodu drukowanego PCB i~podwozia                                           \\ \hline
01.12.2018 - 20.12.2018 & Synteza i~oprogramowanie układów regulacji                                           \\ \hline
20.12.2018 - 01.01.2019 & Złożenie finalnego układu                                                            \\ \hline
01.01.2019 - 20.01.2019 & Strojenie układów regulacji, budowa dokumentacji                                      \\ \hline
	\end{tabular}
	\caption{Harmonogram pracy}
	\label{tab:sched}
\end{table}

\subsection{Budżet}
Budżet projektu wynosił 150 złotych, najbardziej znaczącym wydatkiem w~projekcie było wydrukowanie obwodu elektronicznego.
Zaletą projektu jest modułowość konstrukcji podwozia, przez co~elementy można łatwo wymieniać w~przypadku chęci zastosowania droższych lub tańszych komponentów.
Finalny kosztorys projektu przedstawia tabela \ref{tab:budget}, dokładny spis elementów elektronicznych na~obwodzie drukowanym przedstawiono w~dokumencie \textsc{csv} załączonym do plików projektu.
Całkowity koszt komponentów projektu wyniósł 149,86 złotych.

\begin{table}[hbt]
	\centering
	\begin{tabular}{|c|c|c|c|}
		\hline
		Komponent                                                                                    & Koszt     & Producent                                                           & Dostawca                  \\ \hline
		Obwód drukowany PCB                                                                          & 53,00 PLN    & Elpin PCB                                                           & Elpin PCB                 \\ \hline
		ATmega32u4                                                                                   & 15,91 PLN & Microchip Atmel                                                     & TME Electronic Components \\ \hline
		Elementy pasywne                                                                             & $\backsim$7,50 PLN    & \begin{tabular}[c]{@{}c@{}}Panasonic,\\ ST Electronics\end{tabular} & TME Electronic Components \\ \hline
		Elementy aktywne                                                                             & $\backsim$4,00 PLN     & ST Electronics                                                      & TME Electronic Components \\ \hline
		\begin{tabular}[c]{@{}c@{}}Silniki prądu stałego\\ z kołami i dyskami enkoderów\end{tabular} & 19,90 PLN & Dagu                                                                & Botland                   \\ \hline
		Serwomechanizm                                                                               & 6,90 PLN  & Tower Pro                                                           & Botland                   \\ \hline
		\begin{tabular}[c]{@{}c@{}}Ultradźwiękowy czujnik\\ odległości HC-SR04\end{tabular}          & 7,90 PLN  & Elec                                                                & Botland                   \\ \hline
		Czujniki szczelinowe                                                                         & 9,90 PLN  & Vishay                                                              & Botland                   \\ \hline
		\begin{tabular}[c]{@{}c@{}}Odbiornik podczerwieni\\ TSOP4836 - 36khz\end{tabular}            & 2,95 PLN  & Vishay                                                              & Botland                   \\ \hline
		Bateria Li-Pol                                                                               & 21,90 PLN & Dualsky                                                             & Botland                   \\ \hline
\end{tabular}
	\caption{Kosztorys, rozdysponowanie budżetu}
	\label{tab:budget}
\end{table}

\section{Budowa prototypu, analiza problemów}
Realizację projektu zaczęto od~zgromadzenia peryferiów koniecznych do~realizacji konstrukcji robota.
W~pierwszej fazie prototypowania komponenty testowano osobno używając Arduino Leonardo. Zapoznano się z~ich praktycznymi możliwościami i~działaniem dostępnych bibliotek. 

Następnie połączono wszystkie komponenty i~przeprowadzono ich jednoczesne testy oraz zmierzono zasilanie używając multimetru wraz z~zasilaczem regulowanym.
Elementy prototypowe umieszczono na~platformie testowej i oceniono działanie konstrukcji.
Okazało się, że działanie robota jest możliwe, ale sterowanie silnikami w~torze otwartym nie było wystarczająco precyzyjne aby unikać przeszkód. Przy symetrycznym wysterowaniu silników robot nie poruszał się w~kierunku prostym, różnice w działaniu poszczególnych silników są~zbyt duże by~pracowały one symetrycznie co jest wymagane by platforma jechała na~wprost.
Skręcanie platformy o~zadany kąt również okazało się nieprecyzyjne, obroty o~na~przykład 90~stopni w~prawo były mało powtarzalne i~obarczone dużym błędem.
Zdecydowano się na~syntezę układów regulacji, aby wyeliminować te~problemy.

Testy platformy prototypowej pokazały także, że~złożoność układu jest zbyt duża aby budować go~na~płytce stykowej/prototypowej.
Dodatkowo serwomechanizm, który jest bardzo wrażliwy na~zakłócenia zasilania, działał źle gdy był połączony przez wiele kabli, które razem tworzyły dużą rezystancję. Obserwacje te~skłoniły nas do~zaprojektowania własnego obwodu drukowanego, który mieściłby wszystkie potrzebne komponenty elektroniczne na małej przestrzeni.
Konstrukcja mechaniczna platformy prototypowej okazała się mało solidna i~nie była dostosowana do~używanych przez nas modułów elektronicznych. W~celu zwiększenia  wytrzymałości i~schludności wykonania układu zdecydowano się na~projekt własnego podwozia robota.

\section{Projekt układu elektronicznego}
\subsection{Działanie i uzasadnienie doboru elementów elektronicznych}
\subsubsection{Mikroprocesor ATmega32u4}
Centralnym elementem robota jest mikroprocesor \textsc{avr} o~architekturze \textsc{risc}. Ośmiobitowe mikroprocesory ATmega są~popularnym wyborem przy konstrukcji układów wbudowanych w~przemyśle i~urządzeniach elektronicznych o~niedużym stopniu wymaganej wydajności.
Ich~zaletą jest powszechność oraz fakt,~że~na~procesorach z~tej rodziny bazuje popularna platforma Arduino, w~ramach której dostępny jest szeroki zakres bibliotek programistycznych do~obsługi peryferiów. 

\noindent\begin{minipage}{\linewidth}
Przy wyborze konkretnego modelu mikroprocesora kierowaliśmy się następującymi wymaganiami:
\begin{itemize}
	\item obsługa czterech przerwań zewnętrznych:
		\begin{enumerate}
			\item pochodzących z~enkodera lewego koła,
			\item pochodzących z~enkodera prawego koła,
			\item pochodzących z~czujnika ultradźwiękowego,
			\item pochodzących z~odbiornika podczerwieni, 
		\end{enumerate}
	\item obsługa trzech wyjść PWM, za~pomocą liczników w~celu:
		\begin{enumerate}
			\item sterowania prędkością lewego silnika prądu stałego,
			\item sterowania prędkością prawego silnika prądu stałego,
			\item sterowania położeniem serwomechanizmu, na~którym zamontowany jest czujnik ultradźwiękowy,
		\end{enumerate}
	\item możliwość użycia sumarycznie dwunastu wejść wyjść cyfrowych do~komunikacji z~peryferiami,
	\item pożądana jest wbudowana obsługa komunikacji szeregowej za~pomocą interfejsu USB w~celu łatwego debugowania układu i~zdjęcia pomiarów dynamiki układu przy identyfikacji obiektu regulacji i~strojeniu regulatorów,
	\item powyższe wymagania powinny być spełnione przy użyciu bootloadera i~bibliotek Arduino.
\end{itemize}
\hspace{5mm}
\end{minipage}

Powyższe wymagania spełnia mikroprocesor ATmega32u4 firmy Atmel, co~można wywnioskować z~jego dokumentacji \cite{atmega32u4_datasheet}.
Na~tym procesorze bazuje układ Arduino Leonardo, który wykorzystano przy konstrukcji prototypu.
Mikroprocesor ATmega32u4 z~użyciem bibliotek Arduino pozwala na~używanie do~pięciu przerwań zewnętrznych oraz siedmiu kanałów generujących sygnały \textsc{pwm}.

Istotne jest, że~kanały \textsc{pwm} są~obsługiwane przez cztery oddzielne liczniki. Biblioteki Arduino (szczególnie obsługi serwomechanizmu) wchodzą łatwo w~konflikty i~korzystają z~liczników w~sposób uniemożliwiający ich współdzielenie przy generowaniu sygnałów \textsc{pwm}.
Dlatego przy doborze mikroprocesora i~rozdysponowaniu jego zasobów starano się, aby serwomechanizm był obsługiwany przez oddzielny licznik, który nie jest dzielony z~innymi funkcjami układu.
Oznacza to,~że~pin sterujący serwem~nie powinien generować sygnałów z~użyciem tego samego licznika,~co inne kanały PWM, aby uniknąć konfliktów bibliotek Arduino.

Wybrany model mikroprocesora jest dostępny tylko w~obudowach powierzchniowych \textsc{qfp} (\textit{Quad Flat Package}), przy wyborze tej jednostki należy pamiętać, że wymaga ona umiejętności precyzyjnego lutowania. Procesor może pracować przy zasilaniu 5~\si{\volt}, jest to~dogodna wartość ponieważ reszta peryferiów w~układzie ma~takie same napięcie zasilania.

\subsubsection{Silniki prądu stałego}
Ze względu na ograniczenia budżetowe zdecydowano się na~jedne z najtańszych dostępnych silników, wyprodukowane przez firmę Dagu.
Silniki prądu stałego oferują największe momenty siły przy małych obrotach, nadają się dobrze do~napędzania i~przyspieszania platform robotów, oferują możliwość płynnego sterowania.
Ich wadą jest fakt, że bez dodatkowego układu czujników nie można określić ich kąta obrotu.
Należy mieć na uwadze, że~ze~względu na~obecność komutatora i~szczotek silniki prądu stałego zużywają się w~czasie pracy.
Parametry wybranych przez nas silników są~następujące:
\begin{itemize}
	\item maksymalne napięcie zasilania: 6~\si{\volt},
	\item moment obrotowy: \SI[inter-unit-product =\ensuremath{\cdot}]{0,8}{\kilogram\centi\meter}, \SI[inter-unit-product =\ensuremath{\cdot}]{0,78~}{\newton\meter},
	\item obroty silnika bez obciążenia: $ (90 \pm 10) \ \frac{obr}{min} $,
	\item pobór prądu silnika bez obciążenia: 190~\si{\milli\ampere} (max. 250~\si{\milli\ampere}),
	\item pobór prądu silnika przy zatrzymanym wale: 1~\si{\ampere}.
\end{itemize}
Do silników przymocowano koła o parametrach:
\begin{itemize}
	\item średnicy: 65~\si{\milli\meter},
	\item szerokości: 30~\si{\milli\meter}.
\end{itemize}

\subsubsection{Sterownik silników prądu stałego -  mostek \textsc{h}}
Najbardziej popularnym sposobem sterowania silnikami prądu stałego jest użycie mostka~\textsc{h}.
~Jest to~układ składający się z~czterech tranzystorów polowych, których dreny i~źrodła są~odpowiednio połączone ze~sterowanym silnikiem. Para tranzystorów połączona z~tą samą szczotką silnika ma~złączone bramki, ale przeciwny stan otwarcia.
Złączone bramki są wyprowadzone z~układu i~stanowią wejścia sterowania. W~zależności od tego na które z~wejść podamy stan wysoki przez jeden z~tranzystorów z~każdej pary będzie płynął prąd, powodując obroty silnika w~odpowiednim kierunku.
Układem elektronicznym, który zawiera w sobie dwa mostki~\textsc{h},~co~pozwala na~sterowanie parą silników, jest L298N.
Dodatkowo układ posiada dodatkowe tranzystory do sterowania prędkością silników za pomocą sygnału \textsc{pwm}, który stopniowo otwiera i~domyka tranzystor polowy przepuszczający sygnały wejściowe. Parametry sterownika są~następujące:
\begin{itemize}
	\item maksymalne napięcie zasilania silników: 45~\si{\volt},
	\item napięcie części logicznej: od 4,5~\si{\volt} do 7~\si{\volt},
	\item maksymalny prąd zasilający silnik: 2~\si{\ampere}.
\end{itemize}
Sterownik dostępny jest w~obudowie przewlekanej \textit{Multiwatt15}, jego producentem jest firma STMicroelectronics. Porównując parametry mostka, zawarte w dokumentacji \cite{h_bridge_datasheet} z~parametrami silników możemy stwierdzić, że~jest on~wystarczający do~ich wysterowania.

\subsubsection{Czujnik ultradźwiękowy}
Najbardziej popularnym i~łatwo dostępnym miernikiem odległości jest czujnik ultradźwiękowy HC-SR04.
Czujniki ultradźwiękowe mierzą odległość na~podstawie czasu, który jest potrzebny fali ultradźwiękowej na~dotarcie do~przeszkody i~powrót do~czujnika po~jej odbiciu.
Pomiar czujnikiem rozpoczyna się od~podania na~wejście \textsc{trig} stanu wysokiego przez~10~\si{\micro\second}. Powoduje to~wygenerowanie przez czujnik ciągu ośmiu sygnałów ultradźwiękowych o~częstotliwości 40~\si{\kilo\hertz}. Po~odbiciu sygnału od przeszkody i~jego powrocie do~czujnika odległość można obliczyć według wzoru \ref{eq:ultrasonic}, gdzie:
\begin{itemize}
	\item $ d $ to odległość mierzona,
	\item $ t_h $ to czas trwania stanu wysokiego, 
	\item $ v_s $ to prędkość rozchodzenia się fali dźwiękowej w~powietrzu, typowo 340~\si{\meter\per\second}.
\end{itemize}
\begin{equation}
\label{eq:ultrasonic}
	d = \frac{t_h \cdot v_s}{2}
\end{equation}
Model czujnika HC-SR04, zgodnie z~dokumentacją \cite{ultr_datasheet} charakteryzuje się następującymi parametrami:
\begin{itemize}
	\item napięcie zasilania: 5~\si{\volt},
	\item średni pobór prądu: 15~\si{\milli\ampere},
	\item zakres pomiarowy: od 2~\si{\centi\meter} do 200~\si{\centi\meter},
	\item częstotliwość pracy: 40~\si{\kilo\hertz},
	\item wymiary: $ 45 \times 20 \times 15 $~\si{\milli\meter}.
\end{itemize}
Zasilanie czujnika  i~jego zakres pracy są odpowiednie dla projektu.
Przeszkody, które chcemy wykrywać będą znajdywały się w~odległości parunastu centymetrów od~robota, czyli w~zakresie pracy czujnika.
Należy mieć na uwadze, że~czujniki ultradźwiękowe wykrywają najlepiej duże przeszkody. 
Dodatkowo istotne jest, że~pomiar czujnika ultradźwiękowego trwa w~czasie, przebycie odpowiedniej drogi przez falę ultradźwiękową nie~jest natychmiastowe.
Kwestia ta~zostanie wzięta pod uwagę w~czasie tworzenia oprogramowania.

\subsubsection{Serwomechanizm}
Aby umożliwić robotowi kierowanie czujnika odległości w~różnych kierunkach, został on~zamieszczono na~wieży serwomechanizmu.
Ponieważ wymagamy aby czujnik mógł być skierowany w~lewo, prawo oraz na~wprost wystarczające jest serwo 180 stopni.
Waga czujnika ultradźwiękowego jest znikoma, dlatego serwomechanizm można wybrać kierując się jak najniższą ceną.

\subsubsection{Odbiornik podczerwieni TSOP4836}
Robota wyposażono w~odbiornik podczerwieni ułatwiający jego zatrzymanie.
W celu łatwej współpracy z~domowymi pilotami na~podczerwień należało wybrać odbiornik wspierający popularne formaty: NEC Code, Toshiba Micom Format, Sharp Code, RC5 Code, RC6 Code, R–2000 Code\dots.

Wybraliśmy odbiornik TSOP4836 pracujący z~falami o~częstotliwości 36~\si{\kilo\hertz}. Zgodnie z dokumentacją \cite{ir_datasheet} firmy Vishay
 odbiornika należy go~zabezpieczyć kondensatorem filtrującym i~rezystorem. Parametry odbiornika są~następujące:
\begin{itemize}
	\item napięcie zasilania: od 4,5~\si{\volt} do 5,5~\si{\volt},
	\item średni pobór prądu: 1,5~\si{\milli\ampere}.
\end{itemize}
Przy projektowaniu obwodu drukowanego i~lutowaniu odbiernika należy zwrócić uwagę na jego wyprowadzenia.
Wiele czujników podczerwieni o~identycznych obudowach i~podobnych parametrach ma~bardzo różne kolejności wyprowadzeń.

\subsubsection{Stabilizator napięcia L7805CV}
W konstruowanym projekcie wszystkie układy logiczne zasilane są~napięciem 5~\si{\volt}, natomiast silniki zasilane są napięciem  7,4~\si{\volt}.
Wynika stąd, że~najlepiej zastosować baterię siedmiowoltową, a~zasilanie części logicznej dostarczać poprzez regulator napięcia. Najbardziej popularnym regulatorem jest układ 7805,~produkowany przez firmę STMicroelectronics \cite{stab_datasheet}. 
W wersji \textsc{cv} jego parametry są następujące:
\begin{itemize}
	\item maksymalne napięcie wejściowe: 35~\si{\volt},
	\item napięcie wyjściowe: 5~\si{\volt} (z dokładnością 2 \%),
	\item maksymalny prąd wyjściowy: 1,5~\si{\ampere}.
\end{itemize}
Stabilizator jest dostępny w~różnych obudowach, przewlekanych i~powierzchniowych. Ze~względu na~łatwość montażu, dostępność i~możliwość zamontowania radiatora wybraliśmy model w~obudowie przewlekanej~TO-220.
Po~porównaniu parametrów stabilizatora z~parametrami komponentów, które zasili można stwierdzić, że~jest on~wystarczający by~spełnić zapotrzebowania projektu.

\subsubsection{Akumulator}
Testy pokazały, że~przy zasilaniu 7,4~\si{\volt} układ pobiera prąd~do~0,3~\si{\ampere},~co dostarcza nam informacji potrzebnych do~doboru baterii dla robota.
Zdecydowano się na~zastosowanie akumulatora litowo-polimerowego firmy Dualsky.
Jego najważniejsze parametry są~następujące:
\begin{itemize}
	\item akumulator składa się z dwóch ogniw Li-pol,
	\item napięcie nominalne: 7,4~\si{\volt},
	\item pojemność: 800~\si{\milli\amperehour},
	\item prąd rozładowania ciągły: 20~\si{\ampere},
	\item wbudowane przewody ze wtykiem \textsc{jst}.
\end{itemize}

\subsubsection{Elementy pasywne}
Użyte komponenty elektroniczne wymagają użycia kondensatorów filtrujących, zastosowano kondensatory o~pojemnościach podanych w~dokumentacjach filtrowanych elementów.
Kondensatory ceramiczne są~umieszczone w~obudowach przewlekanych, starano się dobrać kondensatory elektrolityczne w~obudowach powierzchniowych, aby zredukować miejsce, którą zajmują.
Spis wszystkich elementów układu, w~tym elementów pasywnych znajduje się~w osobnym pliku \texttt{csv} dostępnym na stronie projektu.
\subsection{Schemat układu elektronicznego}
\label{sec:schem}

\begin{sidewaysfigure}[!htbp]
		\centering
		
		\caption{Schemat układu elektronicznego}
		\label{fig:sch_eletr}
\end{sidewaysfigure}

Na rysunku \ref{fig:sch_eletr} przedstawiono utworzony schemat układu elektronicznego.
Projekt układu wykonano w~programie Autodesk Eagle\footnote{Autodesk Eagle: \url{https://www.autodesk.com/products/fusion-360/overview}}, korzystając z~bibliotek komponentów. 

Centralnym elementem układu jest mikroprocesor ATmega32u4 oznaczony symbolem \textit{U3}, znajduje się on~w~polu \textit{C3} schematu.
Źródłem taktowania mikroprocesora jest zewnętrzny rezonator kwarcowy 16~\si{\mega\hertz}.
Do~jego poprawnego działania konieczne są~odpowiednie kondensatory.
Aby osiągnąć zamierzone taktowanie użyto kondensatorów o~pojemności 22~\si{\pico\farad}.
Mikroprocesor zasilono napięciem 5~\si{\volt},~które jest filtrowane kondensatorami 0,1~\si{\micro\farad},~zasilanie portu USB jest filtrowane kondensatorami 1~\si{\micro\farad}.
Aby ułatwić restartowanie układu, na schemacie umieszczono przycisk, który umożliwia zwieranie pinu reset z~ziemią.
Jeżeli przycisk jest przytrzymany dostatecznie długo układ mikroprocesorowy zostanie zresetowany.
Aby podczas resetu nie doszło do~zwarcia obwodu zasilania, dodano rezystor \textit{R1}.
Układ resetu znajduje się w~polu \textit{B2} schematu.

W polu \textit{A2} schematu umieszczono diody sygnalizacyjne.
Dioda \textit{PWR\_LED} sygnalizuje obecność napięcia na~wyjściu stabilizatora.
Diody \textit{TX\_LED} oraz \textit{RX\_LED} są związane~z~transmisją szeregową, podłączono je~tak że~są~aktywne kiedy wyjścia procesora są~w~stanie niskim.
Dzięki temu diody świecą kiedy transmisja szeregowa nie ma~miejsca i~sygnalizują tym samym poprawne działanie procesora.
Jest to~wygodne ponieważ dioda \textit{PWR\_LED} sygnalizuje jedynie obecność zasilania układu, ale nie informuje użytkownika o~właściwym uruchomieniu mikroprocesora.
Każda z~diod podłączona jest przez odpowiedni rezystor ograniczający płynący prąd.
W~polu \textit{C1} znajduje się port USB w wersji \textsc{micro}. Linie portu szeregowego zabezpieczono dławikiem ferrytowym, oraz rezystorami.
Do programowania mikroprocesora zastosowano złącze ICSP sześciopinowe, znajdujące się w~polu \textit{D1} schematu.

W~polu \textit{A5} schematu znajduje się mostek L298.
Aby zabezpieczyć układ do~jego wyjść silnikowych dodano diody prostownicze skierowane przeciwnie do~polaryzacji baterii.
W czasie pracy silników na~ich uzwojeniu gromadzi się energia w~postaci pola magnetycznego.
Po zatrzymaniu silników i~hamowaniu platformy energia to wróci do układu w~postaci płynącego prądu.
Dzięki obecności diod układ mostka jest zabezpieczony przez tymi prądami, popłyną one przez diody do~baterii.
 Co więcej, ze~względu na polaryzację diod, energia odzyskiwana z~silników będzie ładować baterię, tworząc prosty układ aktywnego hamowania.
W sekcji \textsc{io ports} znajdują się złącza peryferiów układu.

Komponenty z~fabrycznymi wyprowadzeniami przez goldpiny, połączono takimi samymi złączami od~strony układu.
Silniki i~zasilanie są złączone przez konektory \textsc{arc} dokręcane śrubokrętem.

\subsection{Projekt układu drukowanego}
\subsubsection{Parametry techniczne układu drukowanego}
Ze względu na~ograniczoną przestrzeń na~powierzchni platformy robota zdecydowano się na~wykonanie własnego obwodu drukowanego w~technologii dwustronnej, z~metalizowanymi otworami i~soldermaską.
W celu zachowania zgodności z procesem technologicznym producenta płytek\footnote{Elpin: \url{https://www.elpinpcb.com.pl/prototypy/}}
przyjęto następujące ustawienia \textsc{drc} (\textit{Design rules check}):
\begin{itemize}
	\item grubość laminatu wraz ze~ścieżkami: 1,5~\si{\milli\meter},
	\item grubość ścieżek: 0,035~\si{\milli\meter},
	\item odległości między ścieżkami, przelotkami (\textit{via}) oraz padami: 6~\si{\mil},
	\item odległości ścieżek od~krawędzi płytki: 40~\si{\mil},
	\item minimalna odległość otworów: 6~\si{\mil},
	\item minimalna szerokość ścieżki: 6~\si{\mil},,
	\item minimalna średnica otworu: 0,35~\si{\milli\meter},
	\item szerokość termoizolacji padów od~wylewek (ułatwia lutowanie): 10~\si{\mil}.
\end{itemize}
Dwuwymiarowe wizualizacje obwodu drukowanego wykonanego w~programie Autodesk Eagle przedstawiają rysunki \ref{fig:pcb_top} oraz \ref{fig:pcb_bottom}.
Przy tworzeniu płytki zastosowano technikę wylewki masy, czyli tworzenia dużych płaszczyzn przewodnika, zamiast prowadzenia poszczególnych ścieżek.
Ułatwia to~rozmieszczenie połączeń i~zmniejsza rezystancję ścieżek masy.
Zastosowano materiały zawierające ołów jako bardziej wytrzymałe i~łatwiejsze w~lutowaniu.
W~amatorskim lutowaniu nie używa się temperatur przy których wydzielają się trujące opary ołowiu.
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

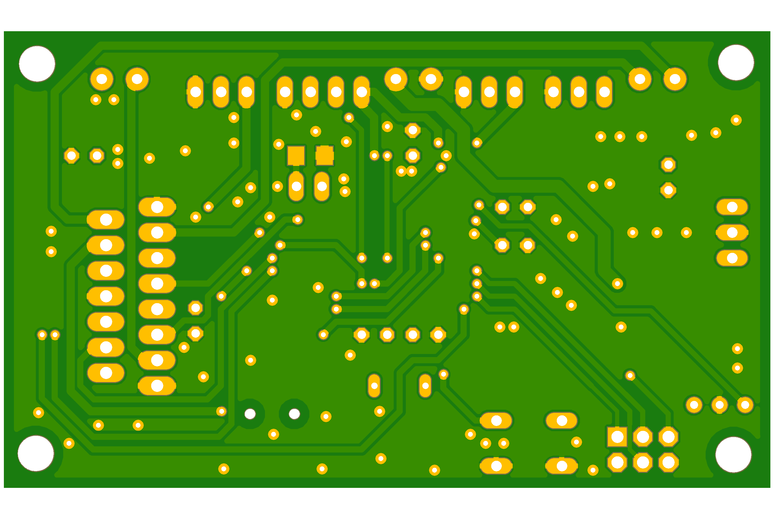
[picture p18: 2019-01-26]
Documentation/Graphics/MazeBot Main Board Bottom.png

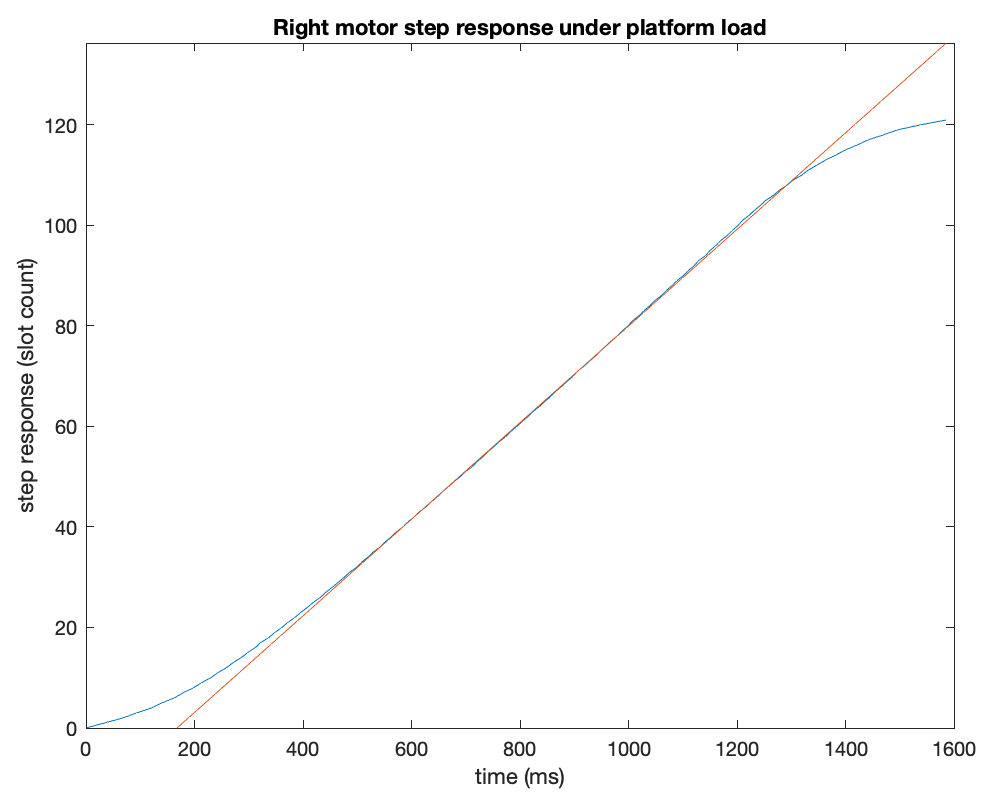
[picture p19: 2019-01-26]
Documentation/Graphics/Identif_right_load.png

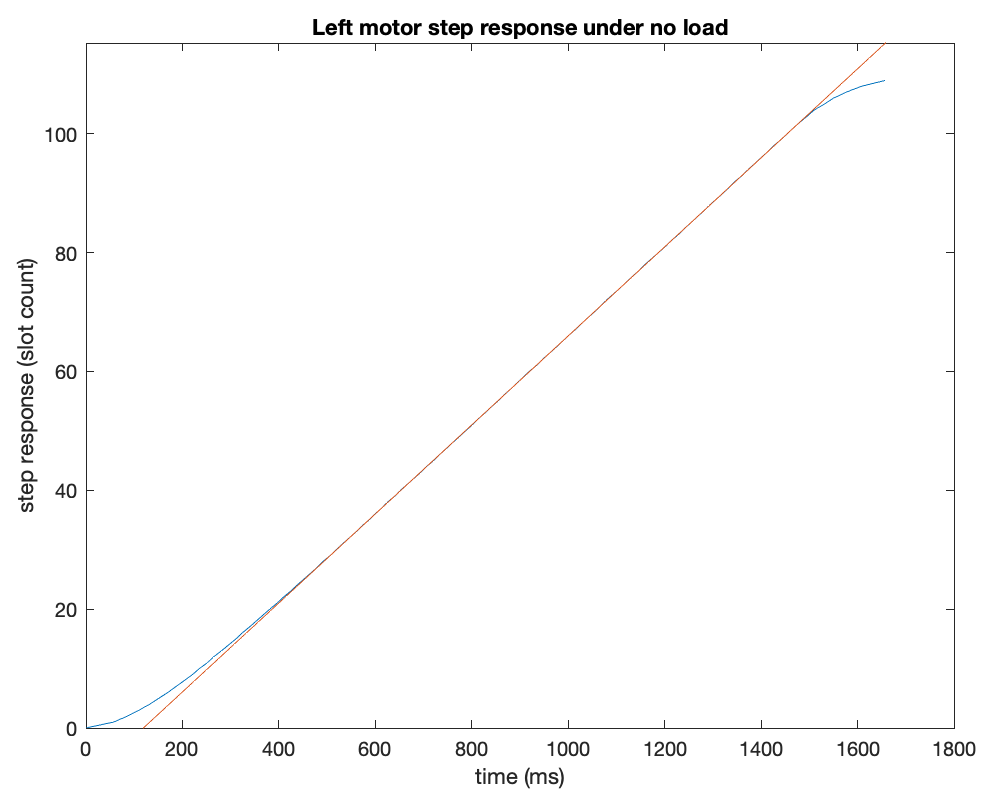
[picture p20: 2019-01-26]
Documentation/Graphics/Identif_left.png

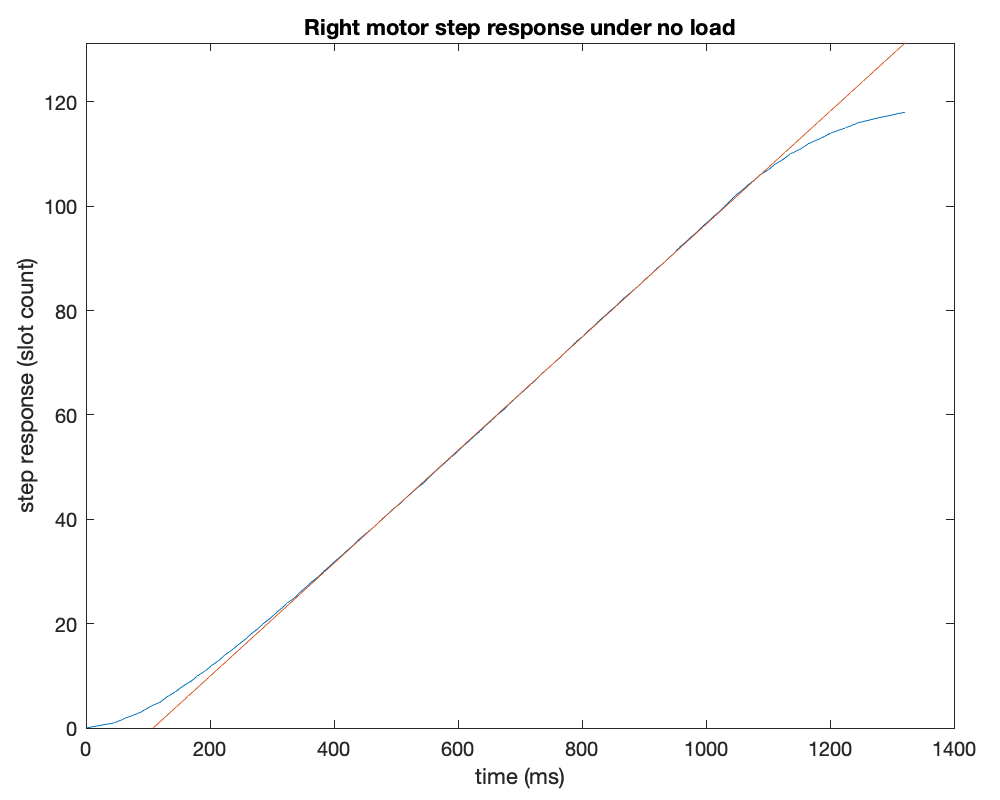
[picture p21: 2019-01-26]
Documentation/Graphics/Identif_right.png

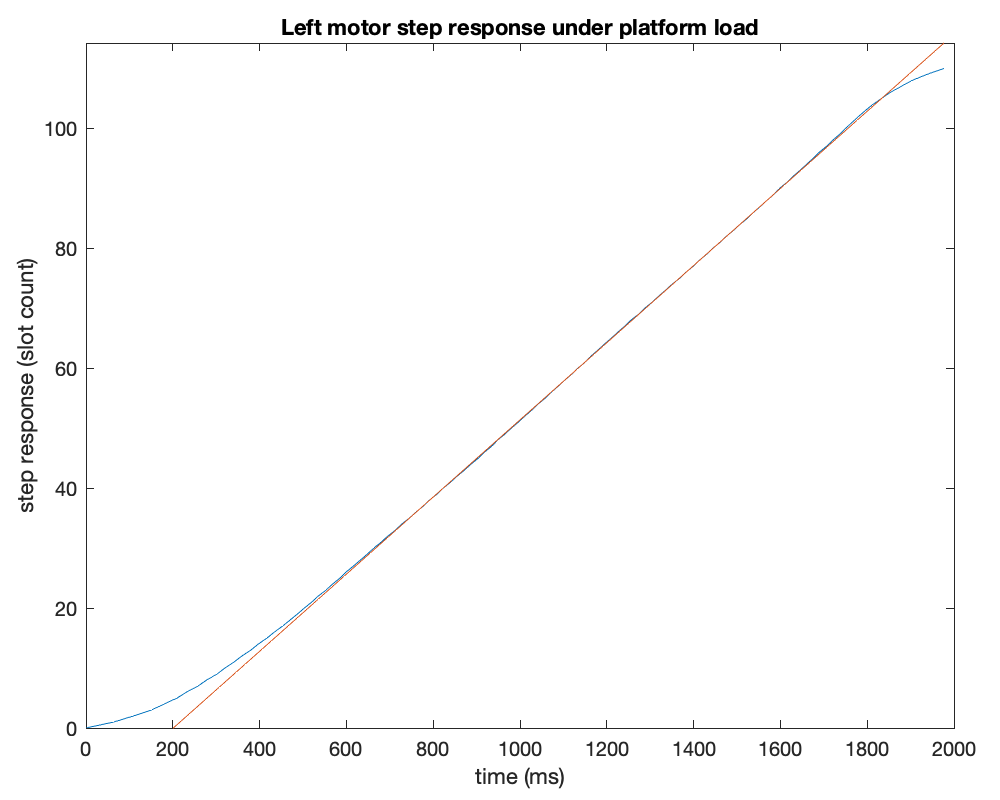
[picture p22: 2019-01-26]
Documentation/Graphics/Identif_left_load.png

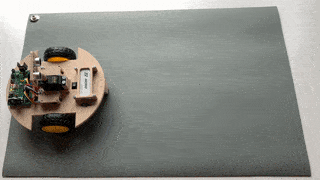
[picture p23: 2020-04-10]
Documentation/Videos/Direction keeping.gif

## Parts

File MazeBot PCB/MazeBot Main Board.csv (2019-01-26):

Part | Value | Device | Package | Description
C1 | 22pF | C-EU025-024X044 | C025-024X044 | CAPACITOR, European symbol
C2 | 22pF | C-EU025-024X044 | C025-024X044 | CAPACITOR, European symbol
C3 | 0.1uF | C-EU025-024X044 | C025-024X044 | CAPACITOR, European symbol
C4 | 0.1uF | C-EU025-024X044 | C025-024X044 | CAPACITOR, European symbol
C5 | 0.33uF | CPOL-EUUD-4X5,8 | UD-4X5,8_NICHICON | POLARIZED CAPACITOR, European symbol
C6 | 0.1uF | C-EU025-024X044 | C025-024X044 | CAPACITOR, European symbol
C7 | 1uF | C-EU025-024X044 | C025-024X044 | CAPACITOR, European symbol
C8 | 0.1uF | C-EU025-024X044 | C025-024X044 | CAPACITOR, European symbol
C9 | 1uF | C-EU025-024X044 | C025-024X044 | CAPACITOR, European symbol
C10 | 4.7uF | CPOL-EUUD-6,3X8,8 | UD-6,3X5,8_NICHICON | POLARIZED CAPACITOR, European symbol
C11 | 47uF | CPOL-EUUD-6,3X8,8 | UD-6,3X5,8_NICHICON | POLARIZED CAPACITOR, European symbol
D1 | GF1 | GF1 | SMA-DO214AC | DIODE
D2 | GF1 | GF1 | SMA-DO214AC | DIODE
D3 | GF1 | GF1 | SMA-DO214AC | DIODE
D4 | GF1 | GF1 | SMA-DO214AC | DIODE
D5 | GF1 | GF1 | SMA-DO214AC | DIODE
D6 | GF1 | GF1 | SMA-DO214AC | DIODE
D7 | GF1 | GF1 | SMA-DO214AC | DIODE
D8 | GF1 | GF1 | SMA-DO214AC | DIODE
HWB |  | JP1E | JP1 | JUMPER
ICSP1 |  | ARDUINO_CONN-ICSP | CONN-2X03 | Arduino ICSP I/O Header
IR_RCV | 38kHz | TSOP38238 | TSOP382 | Vishay Semiconductor TSOP32838 - 38kHz IR Receiver
L1 | 600Ω/500mA | INDUCTOR-0805-3.3UH | 805 | Inductors
MOT_L | 1X2-3.5MM | 1X2-3.5MM | 1X2-3.5MM | 3.5mm Terminal block
MOT_R | 1X2-3.5MM | 1X2-3.5MM | 1X2-3.5MM | 3.5mm Terminal block
PWR_IN | 1X2-3.5MM | 1X2-3.5MM | 1X2-3.5MM | 3.5mm Terminal block
PWR_LED |  | LEDCHIP-LED0805 | CHIP-LED0805 | LED
Q1 | 16MHz | XTAL/S | QS | CRYSTAL
R1 | 10k | RR1206 | R1206 | RESISTOR, European symbol
R2 | 22 | RR1206 | R1206 | RESISTOR, European symbol
R3 | 22 | RR1206 | R1206 | RESISTOR, European symbol
R4 | 1k | RR1206 | R1206 | RESISTOR, European symbol
R5 | 1k | RR1206 | R1206 | RESISTOR, European symbol
R6 | 1k | RR1206 | R1206 | RESISTOR, European symbol
R7 | 10k | RR1206 | R1206 | RESISTOR, European symbol
RX_LED |  | LEDCHIP-LED0805 | CHIP-LED0805 | LED
SERVO |  | MA03-1 | MA03-1 | PIN HEADER
SLOT_L |  | MA03-1 | MA03-1 | PIN HEADER
SLOT_R |  | MA03-1 | MA03-1 | PIN HEADER
SW_RESET |  | 10-XX | B3F-10XX | OMRON SWITCH
TX_LED |  | LEDCHIP-LED0805 | CHIP-LED0805 | LED
U1 | 7805TV | 7805TV | TO220V | Positive VOLTAGE REGULATOR
U2 | L298 | L298 | MULTIWATT-15 | DUAL FULL-BRIDGE DRIVER
U3 | ATMEGA32U4-AU | ATMEGA32U4-AU | TQFP44 | http://www.ladyada.net/library/eagle
ULTR_SENSOR |  | MA04-1 | MA04-1 | PIN HEADER
USB |  | USBMINIB | USB-MINIB | USB Connectors

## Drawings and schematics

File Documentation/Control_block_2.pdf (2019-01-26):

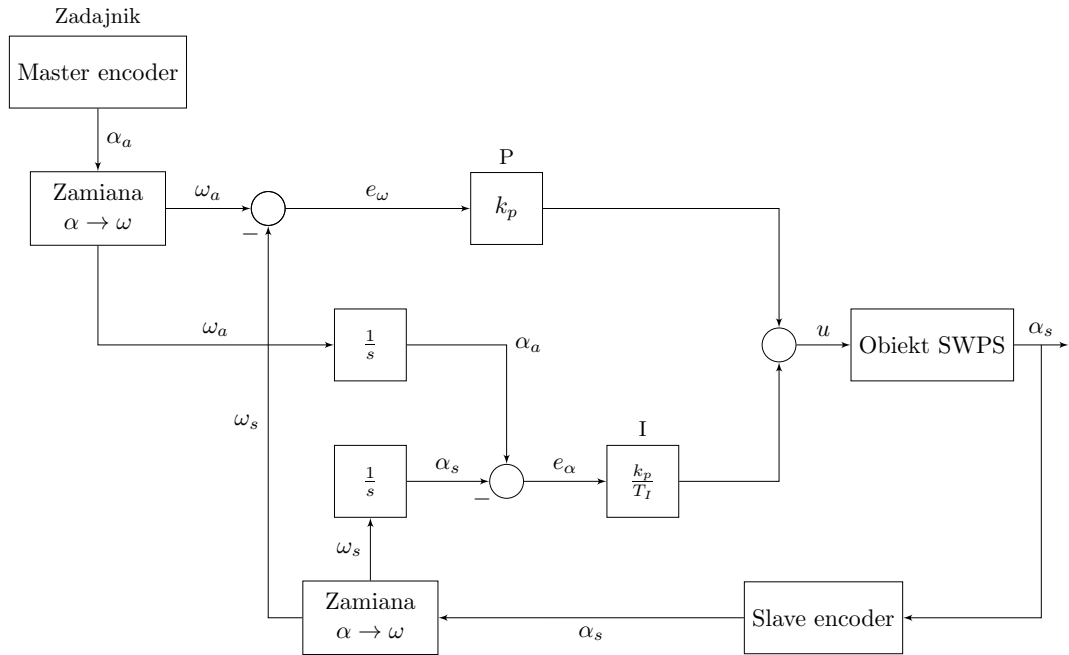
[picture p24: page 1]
Master encoder; Zadajnik; Zamiana α → ω; Obiekt SWPS u; Slave encoder

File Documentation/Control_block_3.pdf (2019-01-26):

−

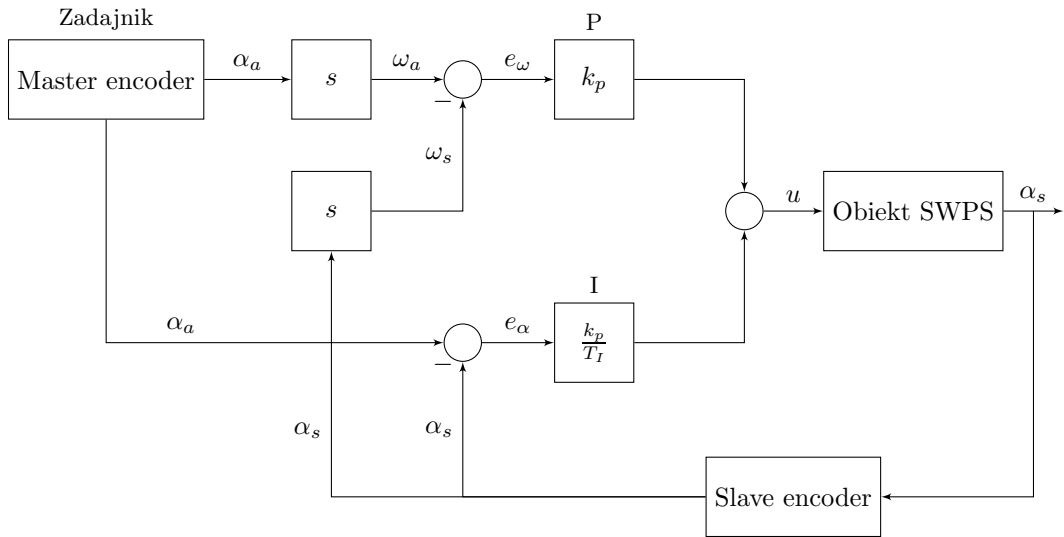
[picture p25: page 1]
Master encoder; Zadajnik; Obiekt SWPS u; Slave encoder

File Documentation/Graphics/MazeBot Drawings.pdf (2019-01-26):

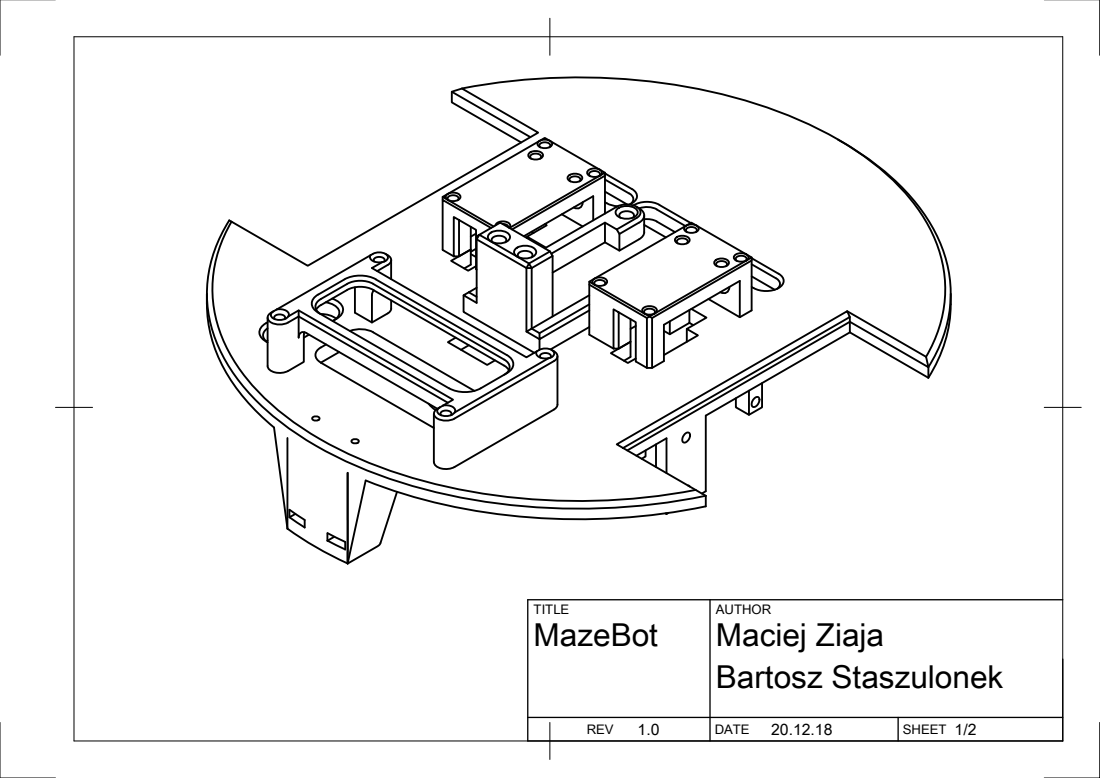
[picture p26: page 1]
MazeBot; Maciej Ziaja; Bartosz Staszulonek

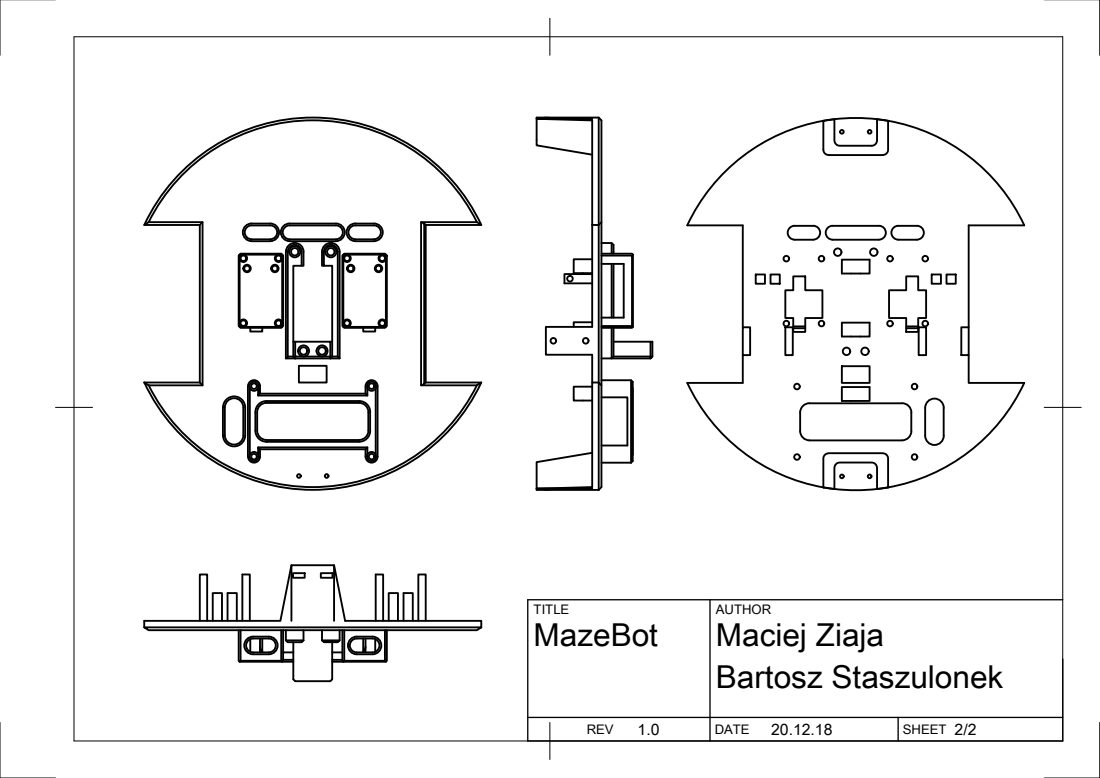
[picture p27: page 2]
Maciej Ziaja Bartosz Staszulonek

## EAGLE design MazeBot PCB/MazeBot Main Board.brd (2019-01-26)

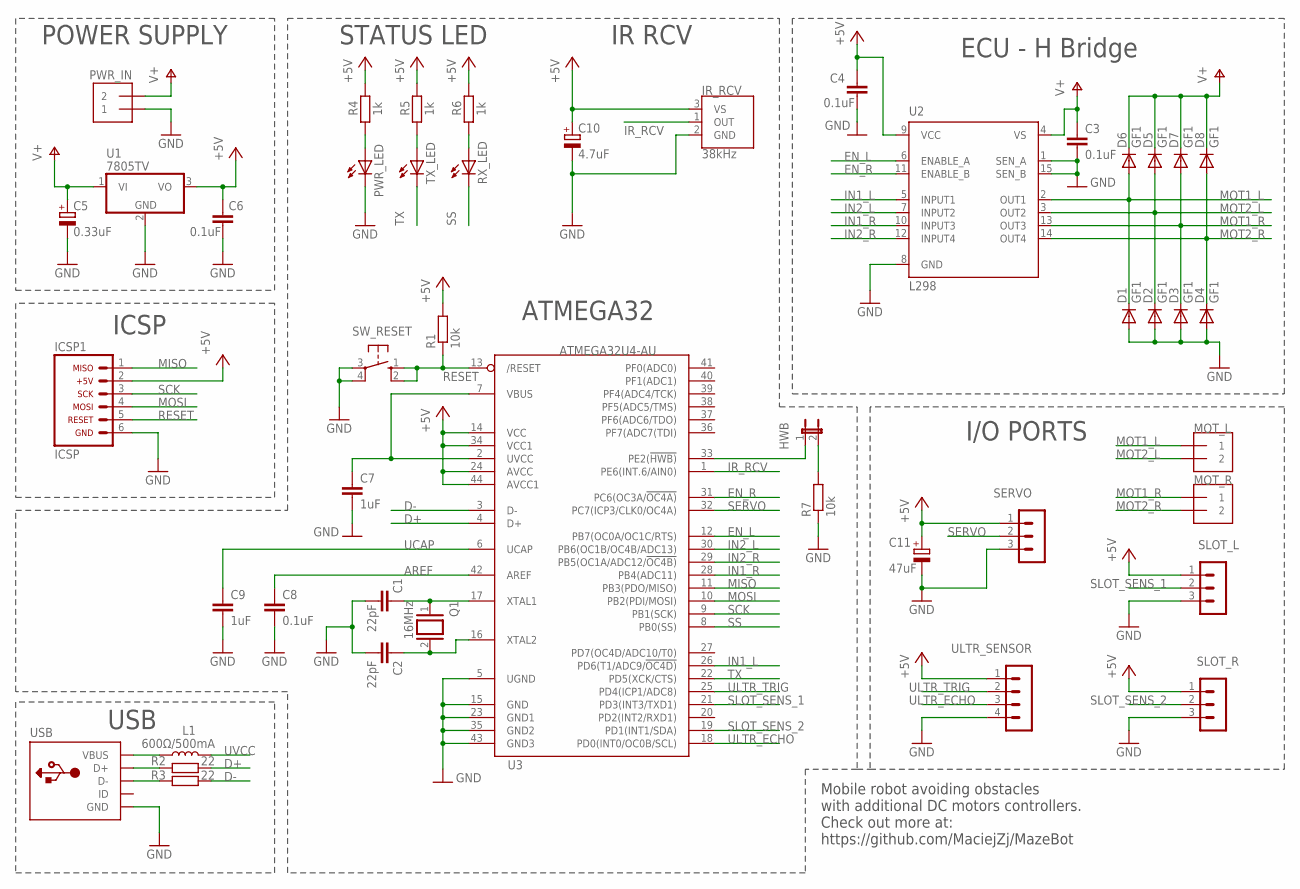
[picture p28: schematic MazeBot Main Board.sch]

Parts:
C1, C2: 22pF; C025-024X044
C3, C4, C6, C8: 0.1uF; C025-024X044
C5: 0.33uF; UD-4X5,8_NICHICON
C7, C9: 1uF; C025-024X044
C10: 4.7uF; UD-6,3X5,8_NICHICON
C11: 47uF; UD-6,3X5,8_NICHICON
D1, D2, D3, D4, D5, D6, D7, D8: GF1; SMA-DO214AC
HWB: JP1E; JP1
ICSP1: ARDUINO_CONN-ICSP; CONN-2X03
IR_RCV: 38kHz; TSOP382
L1: 600Ω/500mA; 0805
MOT_L: 1X2-3.5MM
MOT_R: 1X2-3.5MM
PWR_IN: 1X2-3.5MM
PWR_LED: LEDCHIP-LED0805; CHIP-LED0805
Q1: 16MHz; QS
R1, R7: 10k; R1206
R2, R3: 22; R1206
R4, R5, R6: 1k; R1206
RX_LED: LEDCHIP-LED0805; CHIP-LED0805
SERVO: MA03-1
SLOT_L: MA03-1
SLOT_R: MA03-1
SW_RESET: 10-XX; B3F-10XX
TX_LED: LEDCHIP-LED0805; CHIP-LED0805
U1: 7805TV; TO220V
U2: L298; MULTIWATT-15
U3: ATMEGA32U4-AU; TQFP44
ULTR_SENSOR: MA04-1
USB: USBMINIB; USB-MINIB

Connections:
+5V: C4.1, C6.1, C10.+, C11.+, ICSP1.2, IR_RCV.3 (VS), R1.2, R4.2, R5.2, R6.2, SERVO.1, SLOT_L.1, SLOT_R.1, U1.3 (VO), U2.9 (VCC), U3.14 (VCC), U3.24 (AVCC), U3.34 (VCC1), U3.44 (AVCC1), ULTR_SENSOR.1
AREF: C8.1, U3.42 (AREF)
D+: R2.1, U3.4 (D+)
D-: R3.1, U3.3 (D-)
EN_L: U2.6 (ENABLE_A), U3.12 (PB7(OC0A/OC1C/RTS))
EN_R: U2.11 (ENABLE_B), U3.31 (PC6(OC3A/!OC4A))
GND: C1.1, C2.2, C3.2, C4.2, C5.-, C6.2, C7.2, C8.2, C9.2, C10.-, C11.-, D1.A, D2.A, D3.A, D4.A, ICSP1.6, IR_RCV.2 (GND), PWR_IN.1, PWR_LED.C, R7.1, SERVO.3, SLOT_L.3, SLOT_R.3, SW_RESET.3, SW_RESET.4 (P1), U1.2 (GND), U2.1 (SEN_A), U2.8 (GND), U2.15 (SEN_B), U3.5 (UGND), U3.15 (GND), U3.23 (GND1), U3.35 (GND2), U3.43 (GND3), ULTR_SENSOR.4, USB.GND
IN1_L: U2.5 (INPUT1), U3.26 (PD6(T1/ADC9/!OC4D))
IN1_R: U2.10 (INPUT3), U3.28 (PB4(ADC11))
IN2_L: U2.7 (INPUT2), U3.30 (PB6(OC1B/OC4B/ADC13))
IN2_R: U2.12 (INPUT4), U3.29 (PB5(OC1A/ADC12/!OC4B))
IR_RCV: IR_RCV.1 (OUT), U3.1 (PE6(INT.6/AIN0))
MISO: ICSP1.1, U3.11 (PB3(PDO/MISO))
MOSI: ICSP1.4, U3.10 (PB2(PDI/MOSI))
MOT1_L: D1.K (C), D6.A, MOT_L.1, U2.2 (OUT1)
MOT1_R: D3.K (C), D7.A, MOT_R.1, U2.13 (OUT3)
MOT2_L: D2.K (C), D5.A, MOT_L.2, U2.3 (OUT2)
MOT2_R: D4.K (C), D8.A, MOT_R.2, U2.14 (OUT4)
unnamed: C1.2, Q1.1, U3.17 (XTAL1)
unnamed: C2.1, Q1.2, U3.16 (XTAL2)
unnamed: PWR_LED.A, R4.1
unnamed: R2.2, USB.D+
unnamed: R3.2, USB.D-
unnamed: R5.1, TX_LED.A
unnamed: R6.1, RX_LED.A
unnamed: HWB.1, U3.33 (PE2(!HWB))
unnamed: HWB.2, R7.2
unnamed: L1.1, USB.VBUS
RESET: ICSP1.5, R1.1, SW_RESET.1 (S), SW_RESET.2 (S1), U3.13 (/RESET)
SCK: ICSP1.3, U3.9 (PB1(SCK))
SERVO: SERVO.2, U3.32 (PC7(ICP3/CLK0/OC4A))
SLOT_SENS_1: SLOT_L.2, U3.21 (PD3(INT3/TXD1))
SLOT_SENS_2: SLOT_R.2, U3.19 (PD1(INT1/SDA))
SS: RX_LED.C, U3.8 (PB0(SS))
TX: TX_LED.C, U3.22 (PD5(XCK/CTS))
UCAP: C9.1, U3.6 (UCAP)
ULTR_ECHO: U3.18 (PD0(INT0/OC0B/SCL)), ULTR_SENSOR.3
ULTR_TRIG: U3.25 (PD4(ICP1/ADC8)), ULTR_SENSOR.2
UVCC: C7.1, L1.2, U3.2 (UVCC), U3.7 (VBUS)
V+: C3.1, C5.+, D5.K (C), D6.K (C), D7.K (C), D8.K (C), PWR_IN.2, U1.1 (VI), U2.4 (VS)

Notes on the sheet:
POWER SUPPLY
ECU - H Bridge
ICSP
USB
STATUS LED
ATMEGA32
IR RCV
I/O PORTS
Mobile robot avoiding obstacles with additional DC motors controllers. Check out more at: https://github.com/MaciejZj/MazeBot

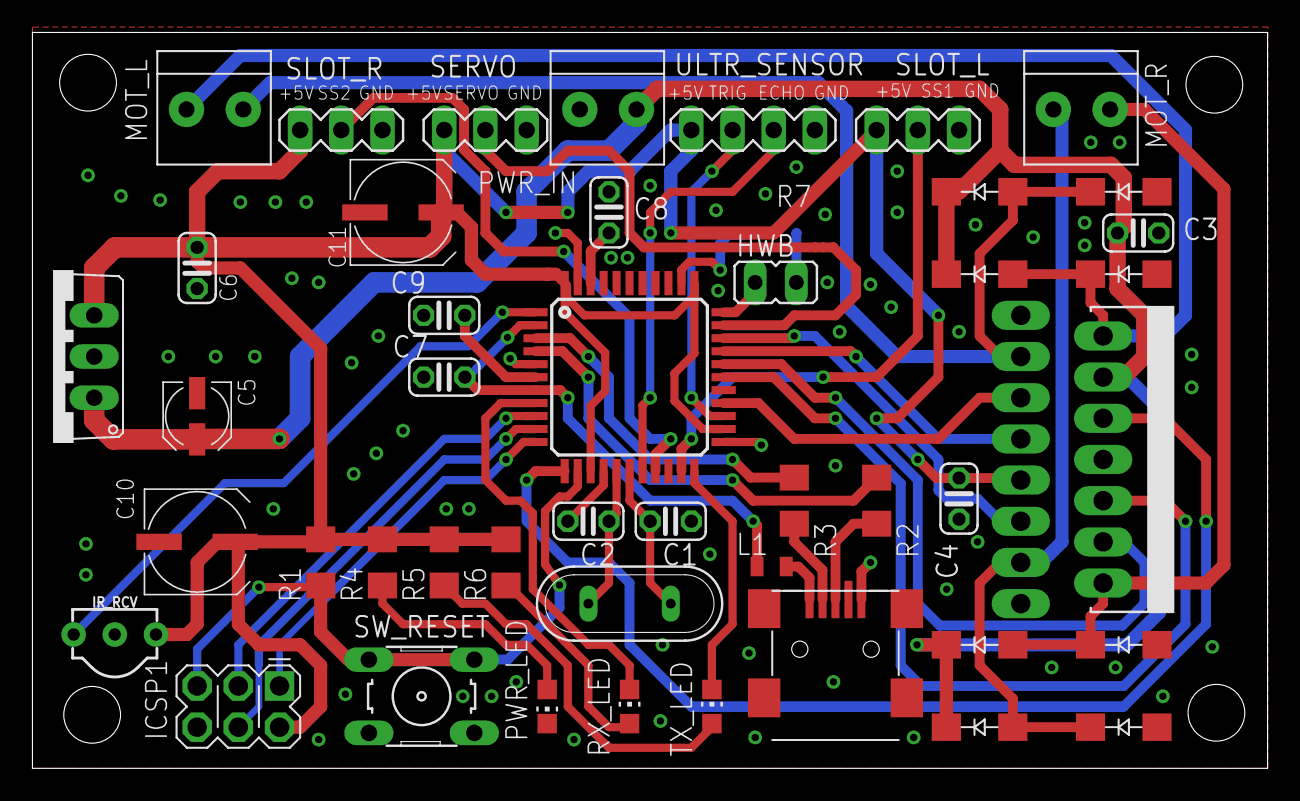
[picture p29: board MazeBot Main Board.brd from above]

Board: 2 copper layers, 76.2 x 45.4 mm, 46 parts (1 on the bottom side), 40 nets.

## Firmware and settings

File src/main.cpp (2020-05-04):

/**
 * \file main.cpp
 * \author Maciej Ziaja, Bartosz Staszulonek
 * \brief Main program logic for MazeBot. Avoids obstacles.
 *
 * Avoids obstacels using ultrasonic sensor and maages servo tower
 * and platform motors. Turns on/off using IR communication.
 * 
 * \see https://github.com/MaciejZj/MazeBot
 */

#include <Arduino.h>
#include <Servo.h>
#include <IRremote.h>
#include "defines.h"
#include "servoSensor.h"
#include "platformMotors.h"
#include "HC_SR04.h"

int motLeftForward = 10;            ///< Left motor forward pin.
int motLeftBack = 12;               ///< Left motor back pin.
int motLeftVelo = 11;               ///< Left motor velocity PWM pin.

int motRightForward = 8;            ///< Right motor forward pin.
int motRightBack = 9;               ///< Right motor back pin.
int motRightVelo = 5;               ///< Right motor velocity PWM pin.

int motLeftSlotSensor = 2;          ///< Left motor slot sensor (encoder) interrupt pin.
int motRightSlotSensor = 1;         ///< Right motor slot sensor (encoder) interrupt pin.
volatile int motLeftCounter = 0;    ///< Counter of left motor's slots detected in current movement.
volatile int motRightCounter = 0;   ///< Counter of right motor's slots detected in current movement.
unsigned long motLeftDeltaTime;     ///< Time betweeen last left enoder's ISRs, indicates velocity.
unsigned long motRightDeltaTime;    ///< Time betweeen last right enoder's ISRs, indicates velocity.

int servoPin = 13;                  ///< Servo control PWM pin.
Servo servoSensor;                  ///< Servo library global instance.

int ultrasonicTrig = 4;             ///< Ultrasonic sensor trigger pin.
int ultrasonicEcho = 3;             ///< Ultrasonic sensor echo pin.
int ultrasonicInt = 0;              ///< Ultrasonic sensor interrupt pin.
HC_SR04 sensor(ultrasonicTrig,      ///< Ultrasonic sensor library instance.
               ultrasonicEcho,
               ultrasonicInt); 

int IRrecvPin = 7;                  ///< IR receiver interrupt and data pin.
IRrecv irrecv(IRrecvPin);           ///< IR library global instance.
decode_results results;             ///< IR received codes holding structure.

volatile int state = START;         ///< State machine state variable.
   
/** @brief Changes the state of program when IR signal is received.
 *
 *  Handles IR receiver interrupt, decodes message and sets new state.
 *
 *  @return Void.
 */
void changeRunningState();

void setup() {
	Serial.begin(9600); // For debug purposes.
	Serial.print("Initialised serial");

	/* Initialise pin modes for motors */
	pinMode(motLeftForward, OUTPUT);
	pinMode(motLeftBack, OUTPUT);
	pinMode(motLeftVelo, OUTPUT);

	pinMode(motRightForward, OUTPUT);
	pinMode(motRightBack, OUTPUT);
	pinMode(motRightVelo, OUTPUT);

	attachInterrupt(digitalPinToInterrupt(motLeftSlotSensor), motorLeftCounterInt, CHANGE);
	attachInterrupt(digitalPinToInterrupt(motRightSlotSensor), motorRightCounterInt, CHANGE);

	/* Initialise servo */
	servoSensor.attach(servoPin);
	turnServoSensor(FRONT);

	/* Initialise ultrasonic sensor */
	sensor.begin();

	/* Enable IR receiver and set it's interrupt */
	irrecv.enableIRIn();
	attachInterrupt(digitalPinToInterrupt(IRrecvPin), changeRunningState, RISING);

	/* Get random seed from analog input 0 */
	randomSeed(analogRead(0));
	
	delay(INITIAL_DELAY);
}

void loop() {
	switch(state) {
		case START:
			resetEncoders();
			headingVeloFix();
			sensor.start();
			state = RUNNING;
			break;

		case RUNNING:
			headingVeloFix();
			if(sensor.isFinished()) {
				if(sensor.getRange() < SAFE_DIST) {
					state = START;

					motorStop();

					int direction = findUnobstructedDirection();
					platformTurn(direction);
				}
				sensor.start();
			}
			break;

		case STOP:
			motorStop();
			state = IDLE;
			break;
	}
}

void changeRunningState() {
	if (irrecv.decode(&results)) {
		unsigned long IRvalue = results.value;
		switch (IRvalue) {
			case 0x100CBCA:
				state = STOP;
				break;
			case 0x1009C9D:
				state = START;
				break;
		}
		irrecv.resume();
	}
}

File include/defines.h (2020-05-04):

/**
* \file defines.h
* \author Maciej Ziaja, Bartosz Staszulonek
* \brief Macros and defines for various MazeBot functions.
*
* \see https://github.com/MaciejZj/MazeBot
*/
 
/* Macros for directions */
#define BACK -1                 ///< Back of platform, where the PCB is.
#define RIGHT 0                 ///< Right side of platform.
#define LEFT 1                  ///< Left side of platform.
#define FRONT 2                 ///< Front of the platform, where the battery is.
 
/* Delay macros */
#define INITIAL_DELAY 3000      ///< Delay between power up and start of run routine.
#define MOTOR_STOP_DELAY 500    ///< Delay after motors stop, ensures stability of platform.
 
#define SAFE_DIST 15            ///< Distance that triggers obstacle detection by ultrasonic.
 
/* State machine macros */
#define IDLE 0                  ///< Idle state in which nothing happens
#define START 1                 ///< Restart encoders, drive motors forward
#define RUNNING 2               ///< Is running now, and avoids obstacles
#define STOP 3                  ///< Stop running, turn off engines, then go idle
 
/* Mechanical parameters */
#define SLOT_NUM 20.0           ///< Number of slots inside of the encoders disks.
#define WHEEL_DIAM 65.0         ///< Diameter of the wheels.
#define WHEELBASE 149.0         ///< Distance between centers of both wheels.
 
/* Macro function calculating number of slots needed to rotate the platform by given angle */
#define SLOT_NUM_FOR_DEG_ROTATION(DEGREE) (round(DEGREE / 360.0 * 2.0 * SLOT_NUM * WHEELBASE / WHEEL_DIAM))
 
/* Enable/disable debug */
#define TURN_ANGLE_DBG 1
#define HEADING_VELO_FIX_DBG 0
 
/* Debug macros */
#define PRINT_HEADING_VELO_FIX_DBG {                                              \
        Serial.println("======= headingVeloFix() debugging =======");             \
        Serial.println("********* master motor debugging *********");             \
        Serial.print("motLeftDeltaTime: "); Serial.println(motLeftDeltaTime);     \
        Serial.print("actuationLeft: "); Serial.println(actuationLeft);           \
        Serial.print("********** slave motor debugging *********");               \
        Serial.print("motRightDeltaTime: "); Serial.println(motRightDeltaTime);   \
        Serial.print("slotDelta: "); Serial.println(slotDelta);                   \
        Serial.print("veloDelta: "); Serial.println(veloDelta);                   \
        Serial.print("actuationRight: "); Serial.println(actuationRight);         \
}
 
#define PRINT_TURN_ANGLE_DBG {                                                                          \
        Serial.println("======= turnAngle() debugging =======");                                        \
        Serial.print("Slot target: "); Serial.println(target);                                          \
        Serial.print("SlotDeltaRight: "); Serial.println(slotDeltaRight);                               \
        Serial.print("SlotDeltaLeft: "); Serial.println(slotDeltaLeft);                                 \
        Serial.println("*************************************");                                        \
        Serial.print("setPointVeloRight: "); Serial.println(setPointVeloRight);                         \
        Serial.print("setPointVeloLeft: "); Serial.println(setPointVeloLeft);                           \
        Serial.println("*************************************");                                        \
        Serial.print("motRightDeltaTime: "); Serial.println(motRightDeltaTime);                         \
        Serial.print("motLeftDeltaTime: "); Serial.println(motLeftDeltaTime);                           \
        Serial.println("*************************************");                                        \
        Serial.print("veloDeltaRight: "); Serial.println(veloDeltaRight);                               \
        Serial.print("veloDeltaLeft: "); Serial.println(veloDeltaLeft);                                 \
        Serial.println("*************************************");                                        \
        Serial.print("compareTime - lastTimeRight: "); Serial.println(compareTime - lastTimeRight);     \
        Serial.print("compareTime - lastTimeLeft: "); Serial.println(compareTime - lastTimeLeft);       \
        Serial.println("*************************************");                                        \
        Serial.print("actuationRight: "); Serial.println(actuationRight);                               \
        Serial.print("actuationLeft: "); Serial.println(actuationLeft);                                 \
}

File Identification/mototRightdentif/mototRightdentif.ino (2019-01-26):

volatile int encoderValue = 0;
unsigned long startTime;
int slotSensor = 1;

int motLeftForward = 10;
int motLeftBack = 12;
int motLeftVelo = 11;


int motRightForward = 8;
int motRightBack = 9;
int motRightVelo = 5;

void count(void);

void setup(){
	Serial.begin(9600);

	pinMode(slotSensor, INPUT);

	pinMode(motLeftForward, OUTPUT);
	pinMode(motLeftBack, OUTPUT);
	pinMode(motLeftVelo, OUTPUT);

	attachInterrupt(digitalPinToInterrupt(slotSensor), count, CHANGE);
}

void loop() {
	delay(3000);
	
	Serial.println("0, 0");
	startTime = millis();
	
	digitalWrite(motLeftForward, HIGH);
	digitalWrite(motLeftBack, LOW);
	analogWrite(motLeftVelo, 100);
	
	digitalWrite(motRightForward, HIGH);
	digitalWrite(motRightBack, LOW);
	analogWrite(motRightVelo, 100);
	while(1){
		if(encoderValue > 100) {
				digitalWrite(motLeftForward, LOW);
				digitalWrite(motLeftBack, LOW);
				analogWrite(motLeftVelo, 0);
				
				digitalWrite(motRightForward, LOW);
				digitalWrite(motRightBack, LOW);
				analogWrite(motRightVelo, 0);
		}
	}
}

void count() {
	static unsigned long lastTime;
	unsigned long timeNow = millis();

	if (timeNow - lastTime < 2) return;

	encoderValue++;
	Serial.print(timeNow - startTime); Serial.print(", "); Serial.println(encoderValue);
	lastTime = timeNow;
}

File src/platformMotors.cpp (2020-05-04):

#include <Arduino.h>
#include "platformMotors.h"
#include "defines.h"

/* Global variables from main file */
extern int motLeftForward;
extern int motLeftBack;
extern int motLeftVelo;

extern int motRightForward;
extern int motRightBack;
extern int motRightVelo;

extern int motLeftCounter;
extern int motRightCounter;

extern unsigned long motLeftDeltaTime;
extern unsigned long motRightDeltaTime;

unsigned long lastTimeLeft;     ///< Time from last interrupt on left endcoder
unsigned long lastTimeRight;    ///< Time from last interrupt on right endcoder

void motorStop() {
	motorLeftStop();
	motorRightStop();
	delay(MOTOR_STOP_DELAY);
}

void motorLeftStop() {
	digitalWrite(motLeftForward, LOW);
	digitalWrite(motLeftBack, LOW);
	analogWrite(motLeftVelo, 0);
}

void motorRightStop() {
	digitalWrite(motRightForward, LOW);
	digitalWrite(motRightBack, LOW);
	analogWrite(motRightVelo, 0);
}

void platformTurn(int direction) {
	switch (direction) {
		case RIGHT:
			platformTurnAngle(-90);
			break;

		case LEFT:
			platformTurnAngle(90);
			break;

		case BACK:
			platformTurnAngle(180);
			break;
	}
}

void platformTurnAngle(int degree) {
	int actuationLeft;       ///< Actuation of the left motor, steers PWM.
	int actuationRight;      ///< Actuation of the right motor, steers PWM.
	float Pv = 1.2;          ///< P coefficient of (subordinate) velocity controller.
	float Iv = 1.2;          ///< I coefficient of (subordinate) velocity controller.
	float Pp = 0.35;         ///< P coefficient of (precedent) position controller.
	float setPointVeloRight; ///< Velocity set point for subordinate controller of right motor.
	float setPointVeloLeft;  ///< Velocity set point for subordinate controller of left motor.
	bool leftIsStopped = false;  ///< Stop indicator for left motor after reaching set point.
	bool rightIsStopped = false; ///< Stop indicator for right motor after reaching set point.

	/* Clear initial values for encoder readouts */
	motLeftDeltaTime = 1;
	motRightDeltaTime = 1;

	motRightCounter = 0;
	motLeftCounter = 0;

	/* Calculate position target (set point) number of slots from given angle */
	float target = abs(SLOT_NUM_FOR_DEG_ROTATION(degree)); 

	/* Calculate direction sign, determines whether platform turns left or right */
	int direction = degree > 0 ? 1 : -1;

	/* Set the last time ISRs as the begging of the work of the controller */
	lastTimeLeft = millis();
	lastTimeRight = millis();

	while(1) {
		int slotDeltaRight = target - motRightCounter;  ///< Error of position (precedent) controller for right motor.
		int slotDeltaLeft = target - motLeftCounter;    ///< Error of position (precedent) controller for left motor.

		/* P regualtor formula, calcualtes velocity setpoint */
		setPointVeloRight = Pp * slotDeltaRight;
		setPointVeloLeft = Pp * slotDeltaLeft;
	
		/* Avoid too high velocity set points to elude wheel slips during long turns */
		if(setPointVeloRight > 16) setPointVeloRight = 16;
		if(setPointVeloLeft > 16) setPointVeloLeft = 16;

		/* Calulate velocity errors */
		float veloDeltaRight = setPointVeloRight - (1.0/((float) motRightDeltaTime));  
		float veloDeltaLeft = setPointVeloLeft - (1.0/((float) motLeftDeltaTime));
		/* Get current time to compare it with last time of ISR and estimate integral */
		unsigned long compareTime = millis();
	
		/* PI controller formula, calculates motors actuations */
		actuationRight = round(Pv * veloDeltaRight + Iv * veloDeltaRight * (compareTime - lastTimeRight));
		actuationLeft = round(Pv * veloDeltaLeft + Iv * veloDeltaLeft * (compareTime - lastTimeLeft));

		/* Prevent oversaturation of PWM */
		if (actuationRight > 255) actuationRight = 255;
		if (actuationLeft > 255) actuationLeft = 255;

		/* If target is reached stop the motor, otherwise actuate it */
		if (motLeftCounter >= target) {
			motorLeftStop(); leftIsStopped = true;
		} else
			motorRotateLeft(direction * actuationLeft);

		if (motRightCounter >= target) {
			motorRightStop(); rightIsStopped = true;
		} else
			motorRotateRight(-direction * actuationRight);
		
		#if TURN_ANGLE_DBG
			PRINT_TURN_ANGLE_DBG
		#endif
		/* If both motors are stopped exit function */
		if(leftIsStopped && rightIsStopped) {
			delay(MOTOR_STOP_DELAY);
			return;
		}
	}
}

void motorRotateLeft(int velocity) {
	if(velocity >= 0) {
		digitalWrite(motLeftForward, HIGH);
		digitalWrite(motLeftBack, LOW);
		analogWrite(motLeftVelo, velocity);
	} else {
		digitalWrite(motLeftForward, LOW);
		digitalWrite(motLeftBack, HIGH);
		analogWrite(motLeftVelo, -velocity);
	}
}

void motorRotateRight(int velocity) {
	if(velocity >= 0) {
		digitalWrite(motRightForward, HIGH);
		digitalWrite(motRightBack, LOW);
		analogWrite(motRightVelo, velocity);
	} else {
		digitalWrite(motRightForward, LOW);
		digitalWrite(motRightBack, HIGH);
		analogWrite(motRightVelo, -velocity);
	}
}

void resetEncoders() {
	motLeftCounter = 0;
	motRightCounter = 0;
	motLeftDeltaTime = 20;
	motRightDeltaTime = 20;
}

void headingVeloFix() {
	int actuationLeft;  ///< Actuation of the left motor, steers the motor's PWM.
	int actuationRight; ///< Actuation of the right motor, steers the motor's PWM.

	float Pm = 10;      ///< Proportional coefficient of master velocity controller.
	float Ps = 15;      ///< Proportional coefficient of slave velocity controller.
	float Is = 5;       ///< Integral coefficient of slave velocity controller.

	/* Master controller */
	float veloDeltaLeft = ((float)200.0/20.0) - (200.0/((float) motLeftDeltaTime));
	actuationLeft = 112 + round(Pm * veloDeltaLeft);
	if(actuationLeft > 255) actuationLeft = 255;

	/* Slave controller */
	float veloDelta = ((200.0/((float) motLeftDeltaTime)) - (200.0/((float) motRightDeltaTime)));
	int slotDelta = motLeftCounter - motRightCounter;
	actuationRight = 88 + round(Ps * veloDelta + Is * slotDelta);
	if(actuationRight > 255) actuationRight = 255;

	/* Actuate motors */
	motorRotateRight(actuationRight);
	motorRotateLeft(actuationLeft);

	#if HEADING_VELO_FIX_DBG
		PRINT_HEADING_VELO_FIX_DBG
	#endif
}

void motorLeftCounterInt() {
	/* When ISR is entered first time in the movement we shouldn't calculate time delta */
	if(motLeftCounter == 0) {
		lastTimeLeft = millis();
		motLeftCounter++; 
		return;
	}

	/** Straightforward low pass filter, debounces the slot sensor 
	 *  when it is on the edge of a slot. 
	 */
	unsigned long timeNow = millis();
	if(timeNow - lastTimeLeft < 2) return;

	/** Increment slot counter and calculate time delta to provide
	 *  information for velocity calculation
	 */
	motLeftCounter++;
	motLeftDeltaTime = timeNow - lastTimeLeft;

	lastTimeLeft = timeNow;
}
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

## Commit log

2018-10-27 Add motor directions defines
2018-10-27 Create servoSensor declarations
2018-10-27 Configure motors GPIO pinout
2018-10-27 Create servoSensor turning function
2018-10-27 Configure servo GPIO pinout
2018-10-27 Fill motors steering functions
2018-10-27 Import HC_SR04 ultrasonic sensor library
2018-10-27 Setup ultrasonic sensor
2018-10-27 Add blocking ultrasonic sensor probing function
2018-10-27 Fix motor functions arguments
    [platformMotors.cpp]
2018-10-27 Fix default arguments in motor functions
    [platformMotors.cpp]
2018-10-30 Fix bugs detected when testing with hardware
    [main.cpp, platformMotors.cpp, servoSensor.cpp]
2018-10-30 Add delay after motor stop
2018-11-02 Create func for IR interrupt
2018-11-02 Disable corridorEscaper till fix
    [main.cpp]
2018-11-11 New pinout and variables for PoC and slot sensors
    Resolves: #18
    [main.cpp]
2018-11-11 Slot sensors setup and counter interrupts
2018-11-12 Split left and right motors stopping
2018-11-12 Add macros for slot numbers calculation
2018-11-22 Add separate motor velocity and direction func
2018-11-27 Heading regulator prototype
2018-11-28 Create Eagle PCB project
2018-11-28 Add stabiliser schematic
    [MazeBot Main Board.sch]
2018-11-28 Add ECU schematic
    [MazeBot Main Board.sch]
2018-11-28 Add ATMEGA with XTAL
    [MazeBot Main Board.sch]
2018-11-28 Add power for ATMEGA
    [MazeBot Main Board.sch]
2018-11-28 Wire ICSP for ATMEGA
    [MazeBot Main Board.sch]
2018-11-29 Add USB schematic
    [MazeBot Main Board.sch]
2018-11-30 Add signal routes
    [MazeBot Main Board.sch]
2018-11-30 Move inside a frame
    [MazeBot Main Board.sch]
2018-11-30 Add status diodes
    [MazeBot Main Board.sch]
2018-11-30 Add IR remote
    [MazeBot Main Board.sch]
2018-11-30 Add IO Ports
    [MazeBot Main Board.sch]
2018-11-30 Fix major ERC issues
    [MazeBot Main Board.sch]
2018-11-30 Create PCB board file
    [MazeBot Main Board.brd]
2018-11-30 Fix minor shematic issues
    [MazeBot Main Board.brd]
2018-11-30 Add power in terminal
    [MazeBot Main Board.brd, MazeBot Main Board.sch]
2018-12-05 Change to SMD and minor fixes
    [MazeBot Main Board.sch]
2018-12-06 Route PCB with SMD
    [MazeBot Main Board.brd, MazeBot Main Board.sch]
2018-12-06 Add mounting screw holes
    [MazeBot Main Board.brd]
2018-12-10 Fix ground connections
    [MazeBot Main Board.brd]
2018-12-10 Fix DRC
    [MazeBot Main Board.brd]
2018-12-10 Fix libraries nums on pads
    [MazeBot Main Board.brd, MazeBot Main Board.sch]
2018-12-10 Add goldpin descriptions
    [MazeBot Main Board.brd]
2018-12-10 Minor fixes
    [MazeBot Main Board.brd]
2018-12-10 Add HWB grounding
    [MazeBot Main Board.brd, MazeBot Main Board.sch]
2018-12-11 Add jumper to HWB
    [MazeBot Main Board.brd, MazeBot Main Board.sch]
2018-12-11 Fix XTAL caps
    [MazeBot Main Board.brd, MazeBot Main Board.sch]
2019-01-02 Final PCB pinout and globals
2019-01-02 Cleanup motor baisc utilities functions
2019-01-02 Turning regulator full draft
2019-01-02 Update slot sensors ISRs
2019-01-02 Enhance straight heding regulator
2019-01-02 Remove old code not based on regulators
2019-01-02 Clear main to match new motors controls
2019-01-02 Upload fixes
    Repairs left encoder ISR, removes inlines and adds delay to turning.
    [platformMotors.cpp]
2019-01-05 PCB print day upload
    [MazeBot Main Board.brd, MazeBot Main Board.sch]
2019-01-05 Import identification files
    [motorLeftIdentif.csv, motorLeftIdentifLoad.csv, motorRightIdentif.csv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]
2019-01-11 Update report PCB and chasis desc
2019-01-18 Add regulators documentation
2019-01-18 Final schamtic cleanup for documentation
    [MazeBot Main Board.brd, MazeBot Main Board.csv, MazeBot Main Board.sch]
2019-01-18 Schematic and PCB images and doc tweaks
2019-01-20 Create tikz flowchart
2019-01-20 Update report to gathered materials
2019-01-26 Fix indentation once more
    [servoSensor.cpp]
2019-02-02 Fix units in doc and finally indentation
    [platformMotors.cpp]

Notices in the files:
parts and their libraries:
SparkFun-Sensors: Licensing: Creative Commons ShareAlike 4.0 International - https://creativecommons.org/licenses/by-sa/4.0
